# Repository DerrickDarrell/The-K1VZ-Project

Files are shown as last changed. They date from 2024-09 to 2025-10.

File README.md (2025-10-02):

# The-K1VZ-Project
THIS REPO IS A WORK IN PROGRESS

## INTRODUCTION
The K1VZ is a heavily modifed Creality K1/K1 Max inspired by [VzBoT](https://github.com/VzBoT3D).
This is a challenging mod with no step-by-step guide. Not for everyone.

Why? Because why the hell not?! If you're still not convinced, this isn't for you.

If you like my work consider [buying me a ko-fi](https://ko-fi.com/derrickdarrell) ☕😊 Your support is greatly appreciated.

## Print Settings
Settings I used for most of the gantry
- 4 walls
- 5 top/bottom
- 50% infill
- Some parts require supports
- Some small parts will require brim





# K1VZ AWD
Figure_sadfh3
Figure_szdfh4

# K1VZ Max AWD
inputshaper_20240913_192055_X
inputshaper_20240913_192055_Y

**THE CONTENTS OF THIS PROJECT FALL UNDER:**
brave_DIrfEC1gKB

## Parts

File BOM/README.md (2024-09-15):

**BOM IS A WORK IN PROGRESS. USE CAD FILE FOR NOW**

https://docs.google.com/spreadsheets/d/11Y8n1dKCBcU4MpgnkywX7PGg8HpcRhKU2c4JyLoFCqU/edit?usp=sharing

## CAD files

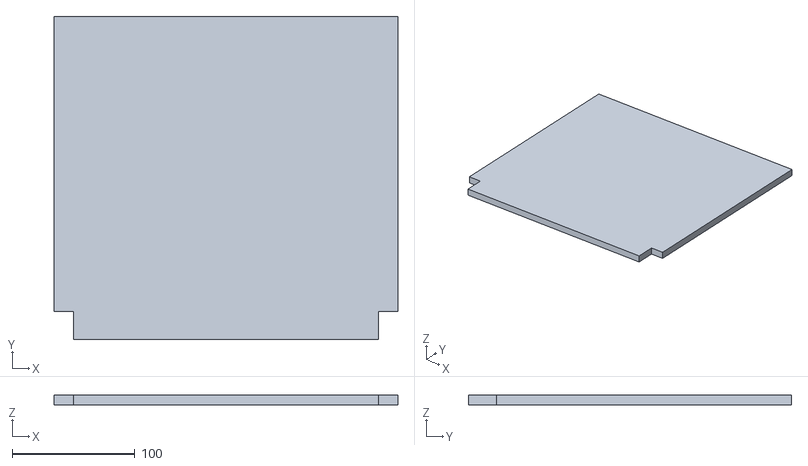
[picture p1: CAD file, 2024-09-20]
CONFIG/Orca/k1vz max awd stock bed area exclusion.stl
280.0 x 263.0 x 8.00

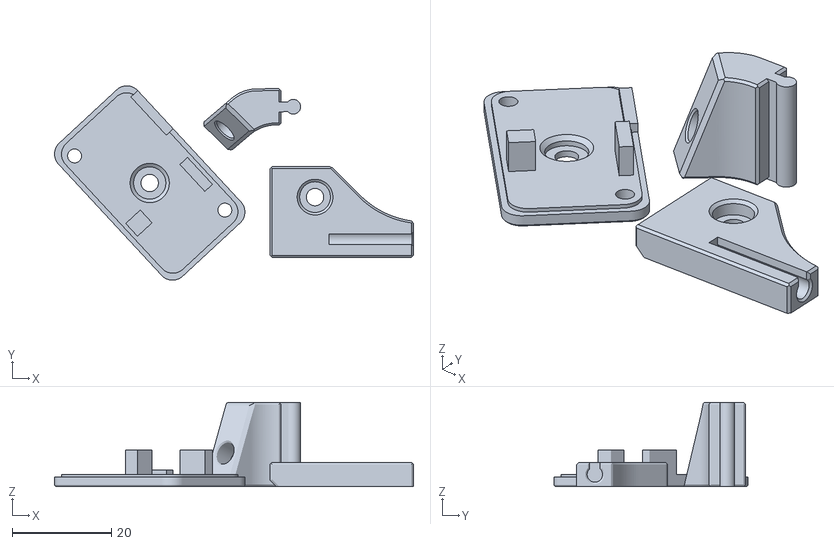
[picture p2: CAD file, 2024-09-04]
STL Files/K1VZ Max/Electronics/K1 Camera Mount/K1 Camera Mount.stl
72.4 x 39.2 x 17.0

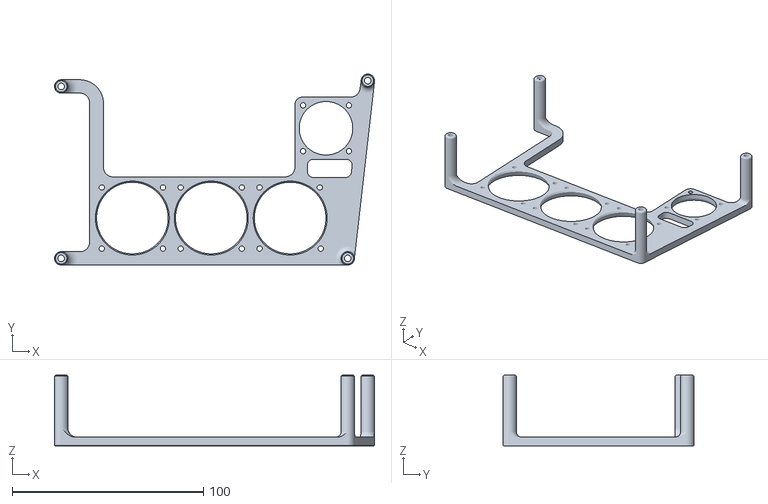
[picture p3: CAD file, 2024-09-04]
STL Files/K1VZ Max/Electronics/M8P/Driver Fan Mount w CM4.stl
167.5 x 100.0 x 37.0

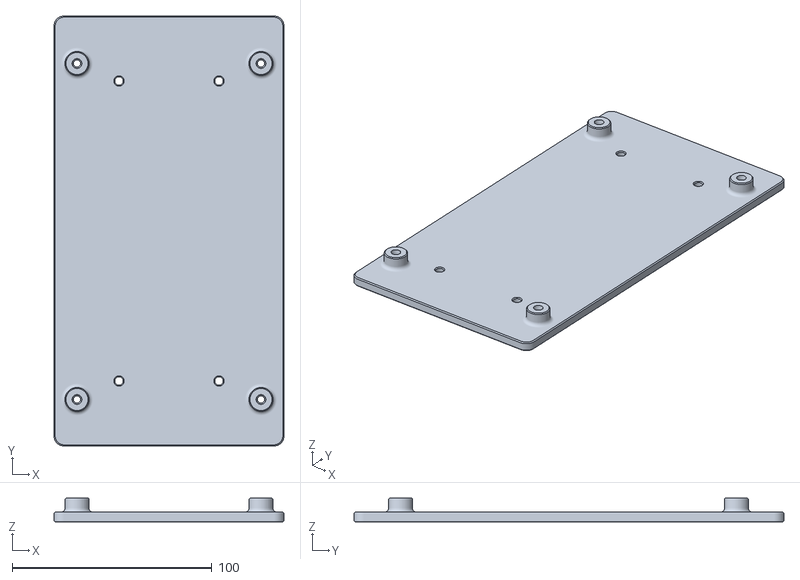
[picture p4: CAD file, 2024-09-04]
STL Files/K1VZ Max/Electronics/Power Supply/Dual LRS-350 - 24V & 48V/Mount.stl
115.0 x 215.0 x 12.0

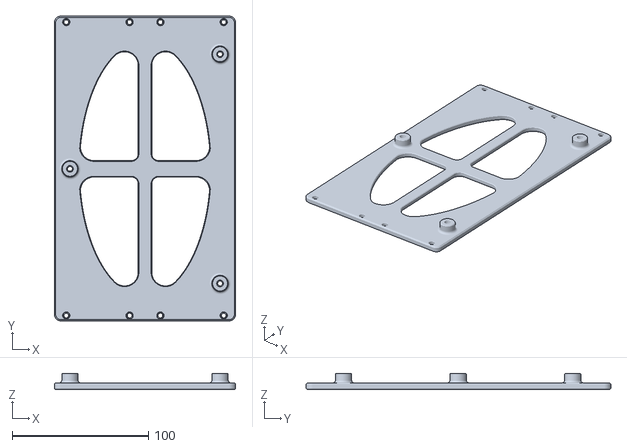
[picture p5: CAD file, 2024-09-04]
STL Files/K1VZ Max/Electronics/Power Supply/Dual UHP-350 - 24V & 48V.stl
133.0 x 223.5 x 12.0

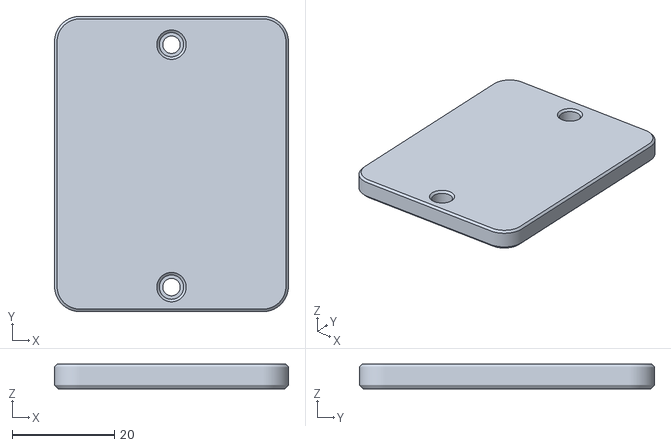
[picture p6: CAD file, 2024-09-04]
STL Files/K1VZ Max/Electronics/SSR Mount - Optional.stl
45.8 x 57.8 x 4.80

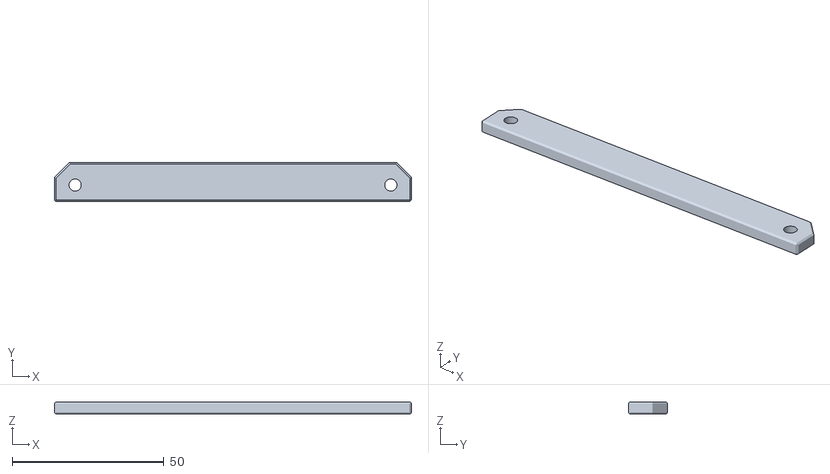
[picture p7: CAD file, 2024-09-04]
STL Files/K1VZ Max/Part Cooling/Aux Fan/Aux Fan Lower Spacer.stl
117.6 x 13.0 x 4.00

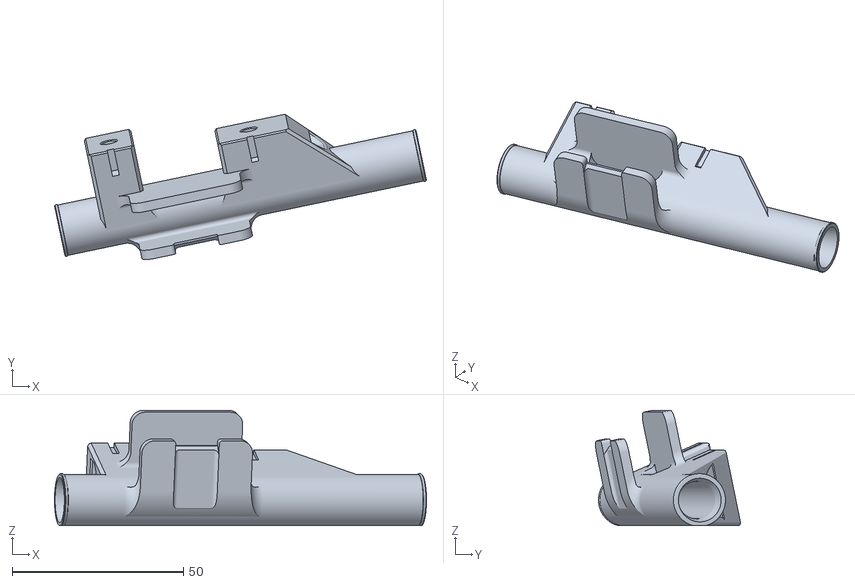
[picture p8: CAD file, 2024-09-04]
STL Files/K1VZ Max/Part Cooling/CPAP/CPAP Hose Belt Bypass.stl
108.6 x 42.3 x 33.7

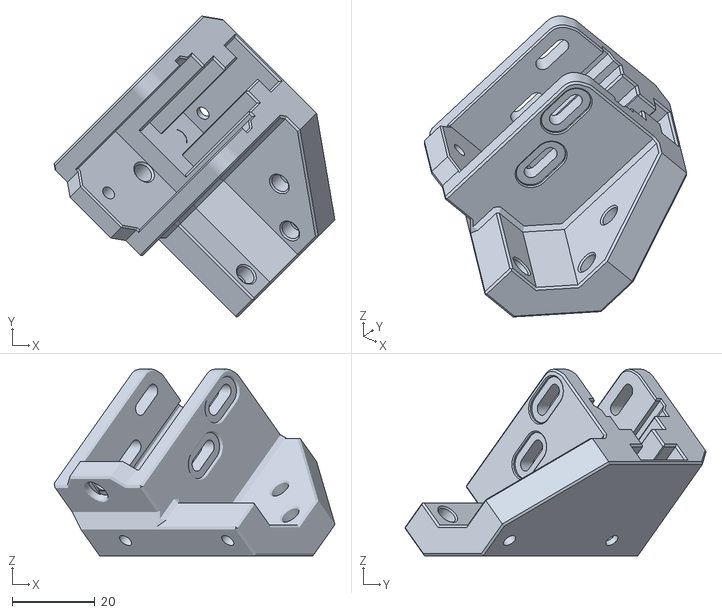
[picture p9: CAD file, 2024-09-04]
STL Files/K1VZ Max/Stepper Mounts/2WD/Front Right Mount.stl
68.0 x 72.9 x 45.2

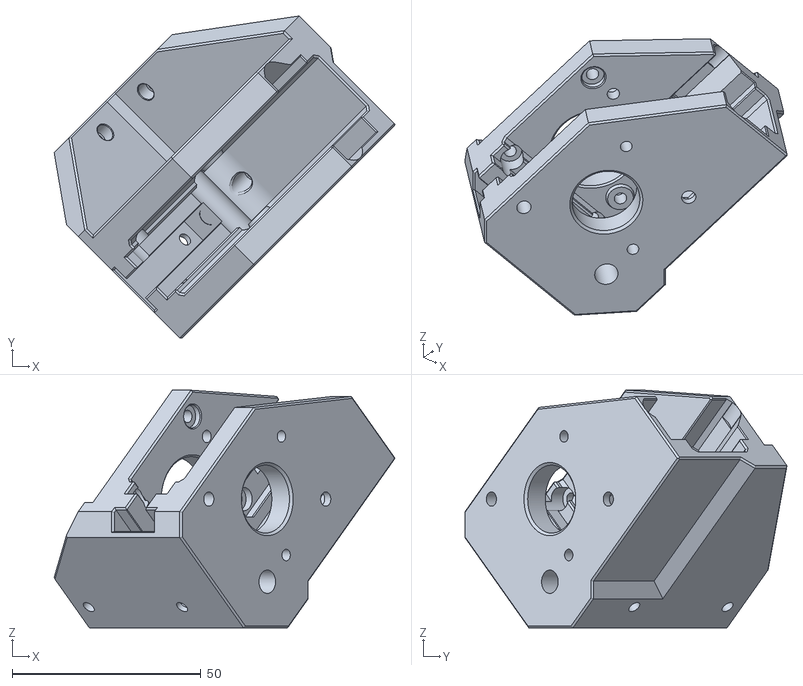
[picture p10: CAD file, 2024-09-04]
STL Files/K1VZ Max/Stepper Mounts/AWD/Rear Left Stepper Mount.stl
90.3 x 85.4 x 63.0

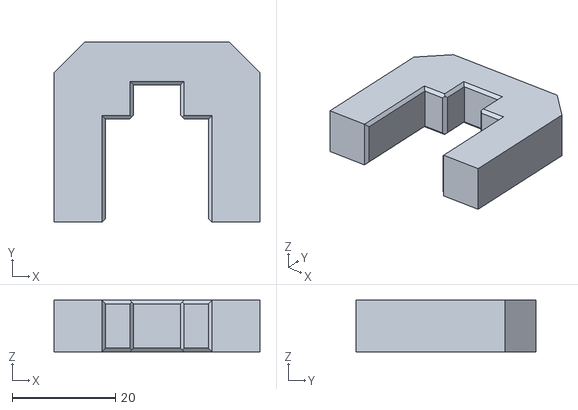
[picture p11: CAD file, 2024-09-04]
STL Files/K1VZ Max/Tools/MGN9 - 2020 Alignment Tool.stl
40.0 x 35.0 x 10.0

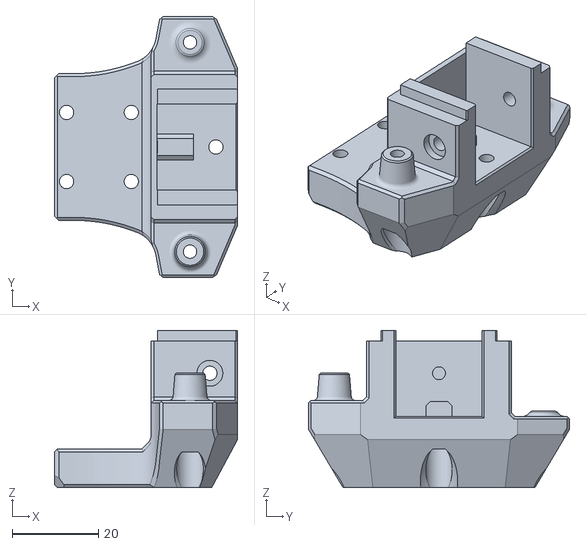
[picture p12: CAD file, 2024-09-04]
STL Files/K1VZ Max/XY Joints/XY Joint Lower w Tooth Idler L.stl
42.4 x 60.5 x 36.4

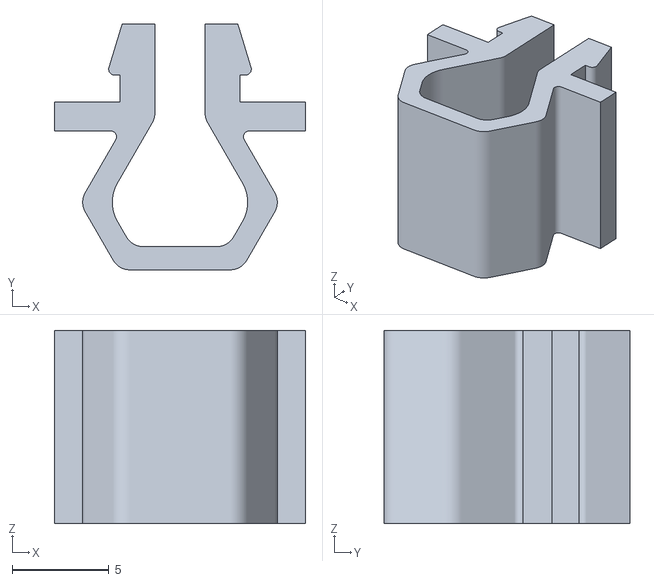
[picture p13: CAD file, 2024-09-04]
STL Files/K1VZ Max/Y Axis/Cable Clips.stl
13.0 x 12.7 x 10.0

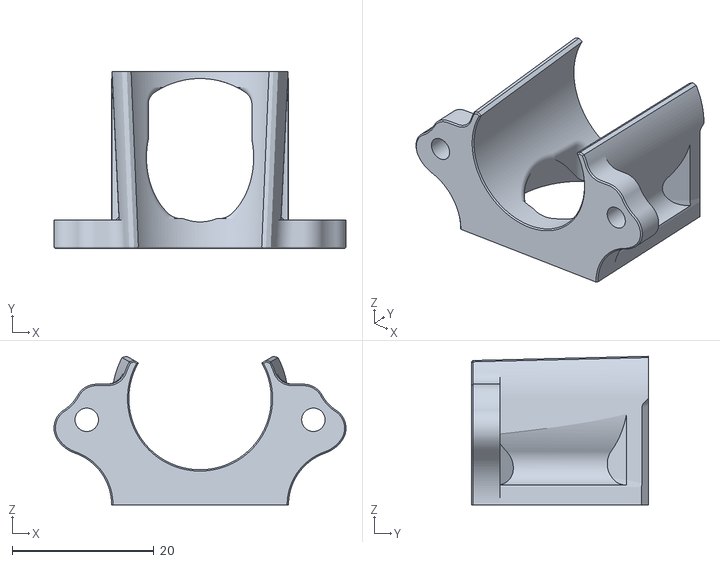
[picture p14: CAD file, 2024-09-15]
STL Files/K1VZ Toolhead/Hotend Fan Shroud (Rapido 2.0 UHF).stl
41.2 x 25.0 x 21.0

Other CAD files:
STL Files/K1VZ/Electronics/M8P/Driver Fan Mount.stl
STL Files/K1VZ/Electronics/Power Supply/UHP-350-24.stl
STL Files/K1VZ Max/Electronics/M8P/Driver Fan Mount.stl
STL Files/K1VZ Max/Electronics/Power Supply/Dual LRS-350 - 24V & 48V/Stack Bracket x2.stl
STL Files/K1VZ Max/Electronics/Power Supply/UHP-350-24 & UHP-500-48.stl
STL Files/K1VZ Max/Electronics/Power Supply/UHP-350-24.stl
STL Files/K1VZ Max/Electronics/WAGOS 5 port - optional.stl
STL Files/K1VZ Max/Part Cooling/CPAP/CPAP Blower 15mm Hose Adapter.stl
STL Files/K1VZ Max/Part Cooling/CPAP/CPAP Blower and Control Board.stl
STL Files/K1VZ Max/Stepper Mounts/2WD/Front Left Mount.stl
STL Files/K1VZ Max/Stepper Mounts/2WD/Rear Left Stepper Mount.stl
STL Files/K1VZ Max/Stepper Mounts/2WD/Rear Right Stepper Mount.stl
STL Files/K1VZ Max/Stepper Mounts/2WD/Standoff x6.stl
STL Files/K1VZ Max/Stepper Mounts/2WD/Tensioner x2.stl
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

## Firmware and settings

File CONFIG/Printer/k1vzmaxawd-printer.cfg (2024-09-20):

############# NOTES ##############

IF USING BEACON, MAKE SURE TO USE 'MESH_OVERSCAN:0' OTHERWISE TOOLHEAD WILL CONTACT THE FRONT MOTOR MOUNTS (AWD)
IF USING CARTO, YOU WILL NEED TO EDIT 'MESH_MIN & MAX' SINCE IT DOES NOT USE 'MESH_OVERSCAN'

############# NOTES ##############



# AWD K1VZ Max by Derrick Darrell
# BTT M8P V2.0

[include mainsail.cfg]
[include macros.cfg]
[include K-ShakeTune/*.cfg]
[virtual_sdcard]
path: /home/pi/printer_data/gcodes
on_error_gcode: CANCEL_PRINT

[mcu]
serial: /dev/serial/by-id/usb-Klipper_stm32h723xx_460033001751313434373135-if00
restart_method: command

[mcu rpi]
serial: /tmp/klipper_host_mcu

[printer]
kinematics: corexy
max_velocity: 1000
max_accel: 50000
max_z_velocity: 15
max_z_accel: 500
square_corner_velocity: 5
minimum_cruise_ratio: 0.0            # dafault: 0.5

[idle_timeout]
timeout: 600

[exclude_object]

[gcode_arcs]
resolution: 0.1

[adxl345]
cs_pin: rpi:None

[resonance_tester]
accel_chip: adxl345
accel_per_hz: 100
probe_points: 140, 132, 10

###############################################################################################################################
# X AXIS
###############################################################################################################################

# MOTOR1
[stepper_x]
step_pin: PB4
dir_pin: PB3
enable_pin: !PB6
microsteps: 32
rotation_distance: 40
endstop_pin: !PF0
position_min: 0
position_max: 280
position_endstop: 280
homing_speed: 80
homing_retract_dist: 0
homing_positive_dir: true

# DRIVER1
[tmc5160 stepper_x]
cs_pin: PB5
# spi_bus: spi3
interpolate: True
# diag1_pin: ^!PF4
sense_resistor: 0.075
spi_software_mosi_pin: PG6
spi_software_miso_pin: PG7
spi_software_sclk_pin: PG8
run_current: 2.25
stealthchop_threshold: 0
# driver_TBL: 1
# driver_TOFF: 3
# driver_DISS2G: 1
# driver_DISS2VS: 1

############################################

# MOTOR2
[stepper_x1]
step_pin: PE2
dir_pin: PE1
enable_pin: !PE4
microsteps: 32
rotation_distance: 40
endstop_pin: !PF0

# DRIVER2
[tmc5160 stepper_x1]
cs_pin: PE3
# spi_bus: spi3
interpolate: True
# diag1_pin: ^!PF3
sense_resistor: 0.075
spi_software_mosi_pin: PG6
spi_software_miso_pin: PG7
spi_software_sclk_pin: PG8
run_current: 2.25
stealthchop_threshold: 0
# driver_TBL: 1
# driver_TOFF: 3
# driver_DISS2G: 1
# driver_DISS2VS: 1

###############################################################################################################################
# Y AXIS
###############################################################################################################################

# MOTOR3
[stepper_y]
step_pin: PB8
dir_pin: PB7
enable_pin: !PE0
microsteps: 32
rotation_distance: 40
endstop_pin: !PC15
position_min: 0
position_max: 263
position_endstop: 263
homing_speed: 80
homing_retract_dist: 0
homing_positive_dir: true

# DRIVER3
[tmc5160 stepper_y]
cs_pin: PB9
# spi_bus: spi3
interpolate: True
# diag1_pin: ^!PF2
sense_resistor: 0.075
spi_software_mosi_pin: PG6
spi_software_miso_pin: PG7
spi_software_sclk_pin: PG8
run_current: 2.25
stealthchop_threshold: 0
# driver_TBL: 1
# driver_TOFF: 3
# driver_DISS2G: 1
# driver_DISS2VS: 1

############################################

# MOTOR4
[stepper_y1]
step_pin: PE6
dir_pin: PE5
enable_pin: !PC14
microsteps: 32
rotation_distance: 40
endstop_pin: !PC15

# DRIVER4
[tmc5160 stepper_y1]
cs_pin: PC13
# spi_bus: spi3
interpolate: True
# diag1_pin: ^!PF1
sense_resistor: 0.075
spi_software_mosi_pin: PG6
spi_software_miso_pin: PG7
spi_software_sclk_pin: PG8
run_current: 2.25
stealthchop_threshold: 0
# driver_TBL: 1
# driver_TOFF: 3
# driver_DISS2G: 1
# driver_DISS2VS: 1

###############################################################################################################################
# Z AXIS
###############################################################################################################################

# MOTOR5
[stepper_z]
step_pin: PG13
dir_pin: PG12
enable_pin: !PG15
microsteps: 32
rotation_distance: 8
gear_ratio: 20:16
endstop_pin: probe:z_virtual_endstop
position_max: 280
position_min: -5
homing_speed: 10
homing_retract_dist: 0                     # Beacon does not require a homing retract. Setting this to something other than 0 will cause occasional erroneous results.

# DRIVER5
[tmc2209 stepper_z]
uart_pin: PG14
interpolate: True
# diag_pin: PD10
run_current: 1.0
sense_resistor: 0.110
stealthchop_threshold: 0

############################################

# MOTOR7
[stepper_z1]
step_pin: PG9
dir_pin: PD7
enable_pin: !PG11
microsteps: 32
rotation_distance: 8
gear_ratio: 20:16
endstop_pin: probe:z_virtual_endstop

# DRIVER7
[tmc2209 stepper_z1]
uart_pin: PG10
interpolate: True
# diag_pin: PD10
run_current: 1.0
sense_resistor: 0.110
stealthchop_threshold: 0

############################################

# MOTOR6
[stepper_z2]
step_pin: PD4
dir_pin: PD3
enable_pin: !PD6
microsteps: 32
rotation_distance: 8
gear_ratio: 20:16
endstop_pin: probe:z_virtual_endstop

# DRIVER6
[tmc2209 stepper_z2]
uart_pin: PD5
interpolate: True
# diag_pin: PD10
run_current: 1.0
sense_resistor: 0.110
stealthchop_threshold: 0

############################################

[z_tilt]
z_positions:
 -50, 0         # stepper_z location (front left)
 330, 0         # stepper_z1 location (front right)
 140, 320       # stepper_z2 location (rear center)
points:
 20, 20         # stepper_z probe location (front left)
 260, 20        # stepper_z1 probe location (front right)
 140, 250       # stepper_z2 probe location (rear center)
speed: 400
horizontal_move_z: 8
retries: 5
retry_tolerance: 0.0075

###############################################################################################################################
# EXTRUDER
###############################################################################################################################

# MOTOR8
[extruder]
step_pin: PC7
dir_pin: !PC8                    # ! for CNC Hextrudort
enable_pin: !PD2
microsteps: 16
# rotation_distance: 5.55        # LGX Lite
rotation_distance: 22            # CNC Hextrudort + 10T
gear_ratio: 50:10                # CNC Hextrudort + 10T
nozzle_diameter: 0.400
filament_diameter: 1.750
heater_pin: PA0
sensor_pin: PB1
sensor_type: PT1000
#control: pid
#pid_Kp: 22.2
#pid_Ki: 1.08
#pid_Kd: 114
min_temp: 0
min_extrude_temp: 0
max_temp: 310
max_extrude_cross_section: 5
max_extrude_only_distance: 200

# DRIVER8
[tmc2209 extruder]
uart_pin: PC6
interpolate: False
run_current: 0.8
sense_resistor: 0.110
stealthchop_threshold: 0

# [firmware_retraction]
# retract_length: 0.6                             #   The length of filament (in mm) to retract when G10 is activated, and to unretract when G11 is activated (but see unretract_extra_length below). The default is 0 mm.
# retract_speed: 45                               #   The speed of retraction, in mm/s. The default is 20 mm/s.
# unretract_extra_length: 0                       #   The length (in mm) of *additional* filament to add when unretracting.
# unretract_speed: 50                             #   The speed of unretraction, in mm/s. The default is 10 mm/s.

###############################################################################################################################
# BED
###############################################################################################################################

[heater_bed]
heater_pin: PA1
sensor_pin: PB0
sensor_type: Generic 3950
#control: pid
#pid_Kp: 37
#pid_Ki: 0.18
#pid_Kd: 280
min_temp: 0
max_temp: 130

###############################################################################################################################
# FANS
###############################################################################################################################

[multi_pin driverfans]
pins: PA4, PF8, PF6

[fan]
pin: rpi:gpio26
hardware_pwm: False
cycle_time: 0.005

[fan_generic Aux_Fan]
pin: PA3
max_power: 1.0
shutdown_speed: 0
#cycle_time:
#hardware_pwm:
kick_start_time: 0.2
off_below: 0.25

[heater_fan hotend_fan]
pin: PF7
max_power: 1.0
shutdown_speed: 1.0

[fan_generic Exhaust_Fan]
pin: PF9
max_power: 1.0

[controller_fan Driver_Fans]
pin: multi_pin:driverfans
max_power: 1.0
heater: extruder, heater_bed
stepper: stepper_x
idle_timeout: 300
idle_speed: 1.0
shutdown_speed: 1.0

###############################################################################################################################
# SENSORS
###############################################################################################################################

[temperature_sensor CM4]
sensor_type: temperature_host

[temperature_sensor M8P V2.0]
sensor_type: temperature_mcu

[temperature_sensor chamber_temp]
sensor_type: EPCOS 100K B57560G104F
sensor_pin: PC5
min_temp: 0
max_temp: 100
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

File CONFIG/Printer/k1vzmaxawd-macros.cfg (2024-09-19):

###############################################################################################################################
# LOAD FILAMENT
###############################################################################################################################

[gcode_macro LOAD_FILAMENT]
gcode:
    {% set speed = params.SPEED|default(300) %}
    {% set max_velocity = printer.configfile.settings['extruder'].max_extrude_only_velocity %}
    SAVE_GCODE_STATE NAME=load_state
    G91
    G92 E0
    G1 E180 F{max_velocity} # fast-load
    G1 E25 F{speed} # purge
    RESTORE_GCODE_STATE NAME=load_state

###############################################################################################################################
# UNLOAD FILAMENT
###############################################################################################################################

[gcode_macro UNLOAD_FILAMENT]
gcode:
    {% set speed = params.SPEED|default(300) %}
    {% set max_velocity = printer.configfile.settings['extruder'].max_extrude_only_velocity %}
    SAVE_GCODE_STATE NAME=unload_state
    G91
    G92 E0
    G1 E25 F{speed} # purge
    G1 E-180 F{max_velocity} # fast-unload
    RESTORE_GCODE_STATE NAME=unload_state

###############################################################################################################################
# PRINT START
###############################################################################################################################

[gcode_macro PRINT_START]
gcode:
  {% set target_bed = params.BED|int %}
  {% set target_extruder = params.EXTRUDER|int %}
  {% set target_chamber = params.CHAMBER|default("40")|int %}
  {% set x_wait = printer.toolhead.axis_maximum.x|float / 2 %}
  {% set y_wait = printer.toolhead.axis_maximum.y|float / 2 %}

  SET_DISPLAY_TEXT MSG="Homing"
  G28                                                   # Full home (XYZ)

  {% if params.BED|int > 90 %}
    SET_DISPLAY_TEXT MSG="Bed: {target_bed}c"           # Displays info

    G1 X{x_wait} Y{y_wait} Z15 F9000                    # Goes to center of the bed
    M190 S{target_bed}                                  # Sets the target temp for the bed

  {% else %}
    SET_DISPLAY_TEXT MSG="Bed: {target_bed}c"           # Displays info
    G1 X{x_wait} Y{y_wait} Z15 F9000                    # Goes to center of the bed
    M190 S{target_bed}                                  # Sets the target temp for the bed
  {% endif %}

  G32                                                   # Home & Z-Tilt

  SET_VELOCITY_LIMIT ACCEL={5000} ACCEL_TO_DECEL={2500}
  BED_MESH_CALIBRATE ADAPTIVE=1                         # Adaptive bed mesh enable. Remove "ADAPTIVE=1"
  SET_VELOCITY_LIMIT ACCEL={printer.configfile.settings.printer.max_accel} ACCEL_TO_DECEL={printer.configfile.settings.printer.max_accel}

  M107                                                 # Turns off partcooling fan

  # Gets ready to print by doing a purge line
  SET_DISPLAY_TEXT MSG="Heating Nozzle: {target_extruder}c & Purging"          # Displays info
  G0 X80 Y0.1 F10000                                     # Moves to starting point
  G0 Z0.2                                              # Raises Z to 0.2
  #M106                                                # Turns on partcooling fan
  M109 S{target_extruder}                              # Heats the nozzle to printing temp
  G91                                                  # Incremental positioning 
  G1 X120 Z0.8 E80 F1000                               # Purge line
  G90                                                  # Absolut position
  SET_DISPLAY_TEXT MSG="K1VZ goes brrrrrrrr"

###############################################################################################################################
# PRINT END
###############################################################################################################################

[gcode_macro PRINT_END]
#   Use PRINT_END for the slicer ending script - please customise for your slicer of choice
gcode:
    # safe anti-stringing move coords
    {% set th = printer.toolhead %}
    {% set x_safe = th.position.x + 20 * (1 if th.axis_maximum.x - th.position.x > 20 else -1) %}
    {% set y_safe = th.position.y + 20 * (1 if th.axis_maximum.y - th.position.y > 20 else -1) %}
    {% set z_safe = [th.position.z + 2, th.axis_maximum.z]|min %}
    
    SAVE_GCODE_STATE NAME=STATE_PRINT_END
    
    M400                           ; wait for buffer to clear
    G92 E0                         ; zero the extruder
    G1 E-10.0 F1800                 ; retract filament
    
    TURN_OFF_HEATERS
    
    G90                                      ; absolute positioning
    G0 X{x_safe} Y{y_safe} Z{z_safe} F20000  ; move nozzle to remove stringing
    G0 X{th.axis_maximum.x//2} Y{th.axis_maximum.y - 15} F3600  ; park nozzle at rear
    M107                                     ; turn off fan

    BED_MESH_CLEAR
    RESTORE_GCODE_STATE NAME=STATE_PRINT_END

###############################################################################################################################
# CANCEL PRINT
###############################################################################################################################

[gcode_macro CANCEL_PRINT]
rename_existing: BASE_CANCEL_PRINT
gcode:
    # safe anti-stringing move coords
    {% set th = printer.toolhead %}
    {% set x_safe = th.position.x + 20 * (1 if th.axis_maximum.x - th.position.x > 20 else -1) %}
    {% set y_safe = th.position.y + 20 * (1 if th.axis_maximum.y - th.position.y > 20 else -1) %}
    {% set z_safe = [th.position.z + 2, th.axis_maximum.z]|min %}
    
    SAVE_GCODE_STATE NAME=STATE_CANCEL_PRINT
    
    M400                           ; wait for buffer to clear
    G92 E0                         ; zero the extruder
    #G1 E-10.0 F1800                 ; retract filament
    
    TURN_OFF_HEATERS
    
    G90                                      ; absolute positioning
    G0 X{x_safe} Y{y_safe} Z{z_safe} F20000  ; move nozzle to remove stringing
    G0 X{th.axis_maximum.x//2} Y{th.axis_maximum.y - 15} F3600  ; park nozzle at rear
    M107                                     ; turn off fan
    
    BED_MESH_CLEAR
    CLEAR_PAUSE
    BASE_CANCEL_PRINT

###############################################################################################################################
# PAUSE
###############################################################################################################################

[gcode_macro PAUSE]
rename_existing: BASE_PAUSE
gcode:
    # Parameters
    {% set z = params.Z|default(10)|int %}                                                   ; z hop amount

    {% if printer['pause_resume'].is_paused|int == 0 %}
        SET_GCODE_VARIABLE MACRO=RESUME VARIABLE=zhop VALUE={z}                              ; set z hop variable for reference in resume macro
        SET_GCODE_VARIABLE MACRO=RESUME VARIABLE=etemp VALUE={printer['extruder'].target}    ; set hotend temp variable for reference in resume macro

        SAVE_GCODE_STATE NAME=PAUSE                                                          ; save current print position for resume
        BASE_PAUSE                                                                           ; pause print
        {% if (printer.gcode_move.position.z + z) < printer.toolhead.axis_maximum.z %}       ; check that zhop doesn't exceed z max
            G91                                                                              ; relative positioning
            G1 Z{z} F900                                                                     ; raise Z up by z hop amount
        {% else %}
            { action_respond_info("Pause zhop exceeds maximum Z height.") }                  ; if z max is exceeded, show message and set zhop value for resume to 0
            SET_GCODE_VARIABLE MACRO=RESUME VARIABLE=zhop VALUE=0
        {% endif %}
        G90                                                                                  ; absolute positioning
        G1 X{printer.toolhead.axis_maximum.x/2} Y{printer.toolhead.axis_minimum.y+5} F6000   ; park toolhead at front center
        SAVE_GCODE_STATE NAME=PAUSEPARK                                                      ; save parked position in case toolhead is moved during the pause (otherwise the return zhop can error)
        M104 S0                                                                              ; turn off hotend
        SET_IDLE_TIMEOUT TIMEOUT=43200                                                       ; set timeout to 12 hours
    {% endif %}

###############################################################################################################################
# RESUME
###############################################################################################################################
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

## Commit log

2024-09-04 Upload CAD FIles
2024-09-04 Update Belt Path
2024-09-04 STL Upload
    [Aux Fan Lower Spacer.stl, Belt Clamp x4.stl, CPAP Blower 15mm Hose Adapter.stl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]
2024-09-04 Update K1VZ Max Gantry.zip
2024-09-04 Create MGN9H - Toolhead Spacer.stl
    [MGN9H - Toolhead Spacer.stl]
2024-09-14 Update Toolhead
    Added Rapido hotend
    More compact toolhead/cpap ducting
    Separated Toolhead CAD File from Gantry
    [ADXL345 Mount.stl, Belt Clamp x4.stl, CPAP Hose Clamp.stl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]
2024-09-15 Added Rapido 2.0 UHF Fan Shroud
    [Hotend Fan Shroud (Goliath).stl, Hotend Fan Shroud (Rapido 2.0 UHF).stl, Hotend Fan Shroud.stl]
2024-09-15 config files - reference only
    [k1vz2wd-macros.cfg, k1vz2wd-printer.cfg, k1vzmaxawd-macros.cfg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]
2024-09-20 Orca Slicer
    Added stock bed area exclusion for front motor mounts (AWD only)
    [k1vz max awd stock bed area exclusion.stl, k1vz2wd-macros.cfg, k1vz2wd-printer.cfg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]
